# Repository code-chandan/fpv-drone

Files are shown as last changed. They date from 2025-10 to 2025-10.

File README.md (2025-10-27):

# Aero FPV Drone

Aero is that one FPV drone you design in your head during boring lectures and then actually build when you finally have the time and brainpower. It’s a freestyle rig that’s super lightweight, fully custom, and made to do flips, dives, and maybe crash a few times without crying.

This thing isn’t printed yet, btw. The model is locked and loaded in Fusion 360. 

---

## Frame Preview

| Image | Description |
|---|---|
|  | Full Fusion 360 render of the frame. All parts modeled to scale with 5" props |

---

## what came into my mind when i designed it

Aero was designed from scratch in Fusion 360 with the idea of keeping things modular, fixable, and crash-forgiving. The frame uses custom top and bottom plates that can either be 3D printed in PLA+ or laser-cut in carbon fiber if budget allows. The arms are separated for easier swaps when the inevitable faceplant happens. Every screw, standoff, and capacitor has its space.

It’s got that “I-built-this-in-my-room” energy but backed by a parts list that can punch with the big brands. The wiring is gonna be clean thanks to the 4-in-1 ESC stack, and the VTX and analog cam give it old-school FPV vibes without sacrificing clarity.

---
## diy transmitter and receiver 

| Image | Description |
|---|---|
|  | diy transmitter |

| Image | Description |
|---|---|
|  | controller case |

| Image | Description |
|---|---|
|  | diy receiver  |

| Image | Description |
|---|---|
|  | flight controller ( more layers cus so much routing) |

---
## Tech Specs

- Motor-to-motor distance fits 5-inch props  
- 2207 2400KV motors 
- 4-in-1 ESC (30A) with solder tabs facing up  
- Power distribution through a separate PDB  
- XT60 battery input with a 470uF cap for that ripple control  
- GPS module slot for Return-To-Home  
- Space for analog FPV cam + VTX  
- Foam landing pads and battery strap support

---

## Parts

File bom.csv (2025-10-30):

Product | Price per Unit | Qty | Estimated Price (USD) | Link
2207 2400KV brushless motors | $13.63 | 4 | $54 | https://robu.in/product/sunfun-d2207-2600kv-bldc-motor
4-in-1 ESC 30A | $35.00 | 1 | $35.00 | https://robocraze.com/products/speedybee-f405-bls-50a-30x30-4-in-1-esc
PCB(JLCPCB) | $154 | 1 | $154
Arms (petg-cf)(own expense) | NIL | 4 | NIL
Top Plate (petg-cf)(own expense) | NIL | 4 | NIL
Bottom Plate (petg-cf)(own expense) | NIL | 4 | NIL
M3 Screws | $6.00 | 1 | $6.00 | https://robu.in/product/easymech-ss-304-pan-philips-head-m3-x-5-mm-bolt-25-pcs
5-inch Tri-blade Props | $2 | 4 | $8.00 | https://robocraze.com/products/9450-carbon-fiber-propeller-for-f450-f550-drone-1-pair
XT60 Connector | $1.20 | 1 | $1.20 | https://www.amazon.in/Invento-8944638611431-Female-Connectors-Battery/dp/B06Y6NRP5T
Power Distribution Board | $4.00 | 1 | $4.00 | https://robu.in/product/cc3d-power-distribution-board-dual-bec-lc-filter-led-switch
Capacitor (35V 470uF) | $2.50 | 2 | $2.50 | https://amzn.in/d/glLVvrR
Battery Strap | NIL | 1 | NIL
LiPo Battery 4S 1500mAh 100C | $19.97 | 1 | $19.97 | https://amzn.in/d/bcKfxz0
Video Transmitter (VTX) | $23 | 1 |  | https://robu.in/product/hglrc-zeus-nano-vtx-350mw-16x16-20x20-25-5x25-5mm
Antenna (VTX) | $7.11 | 1 | $7.11 | https://www.drkstore.in/flywoo-5-8ghz-light-5-8g-3dbi-brass-antenna-ufl-for-vtx/
GPS Module | $20 | 1 | $20 | https://www.drkstore.in/flyfishrc-m10-mini-gps-module/
Buzzer with LED | NIL | 1 | NIL
Foam Landing Pads | NIL | 1 | NIL
Heat Shrink Tubing | $4.00 | 1 | $4.00 | https://robocraze.com/products/530-pcs-color-shrink-tube-wire-insulation-sleeve
Silicone Wires (14AWG, 20AWG) | $3.00 | 1 | $3.00 | https://robocraze.com/products/xt60-female-connector-with-silicon-wire
Flight Stack Mounting Grommets | $1.50 | 1 | $1.50 | https://amzn.in/d/hn6yIDM
TOTAL |  |  | $262

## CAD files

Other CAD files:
cad/aero.step
cad/aero controller.f3d

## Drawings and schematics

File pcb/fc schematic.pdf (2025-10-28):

# GND¹

## SWD ¹

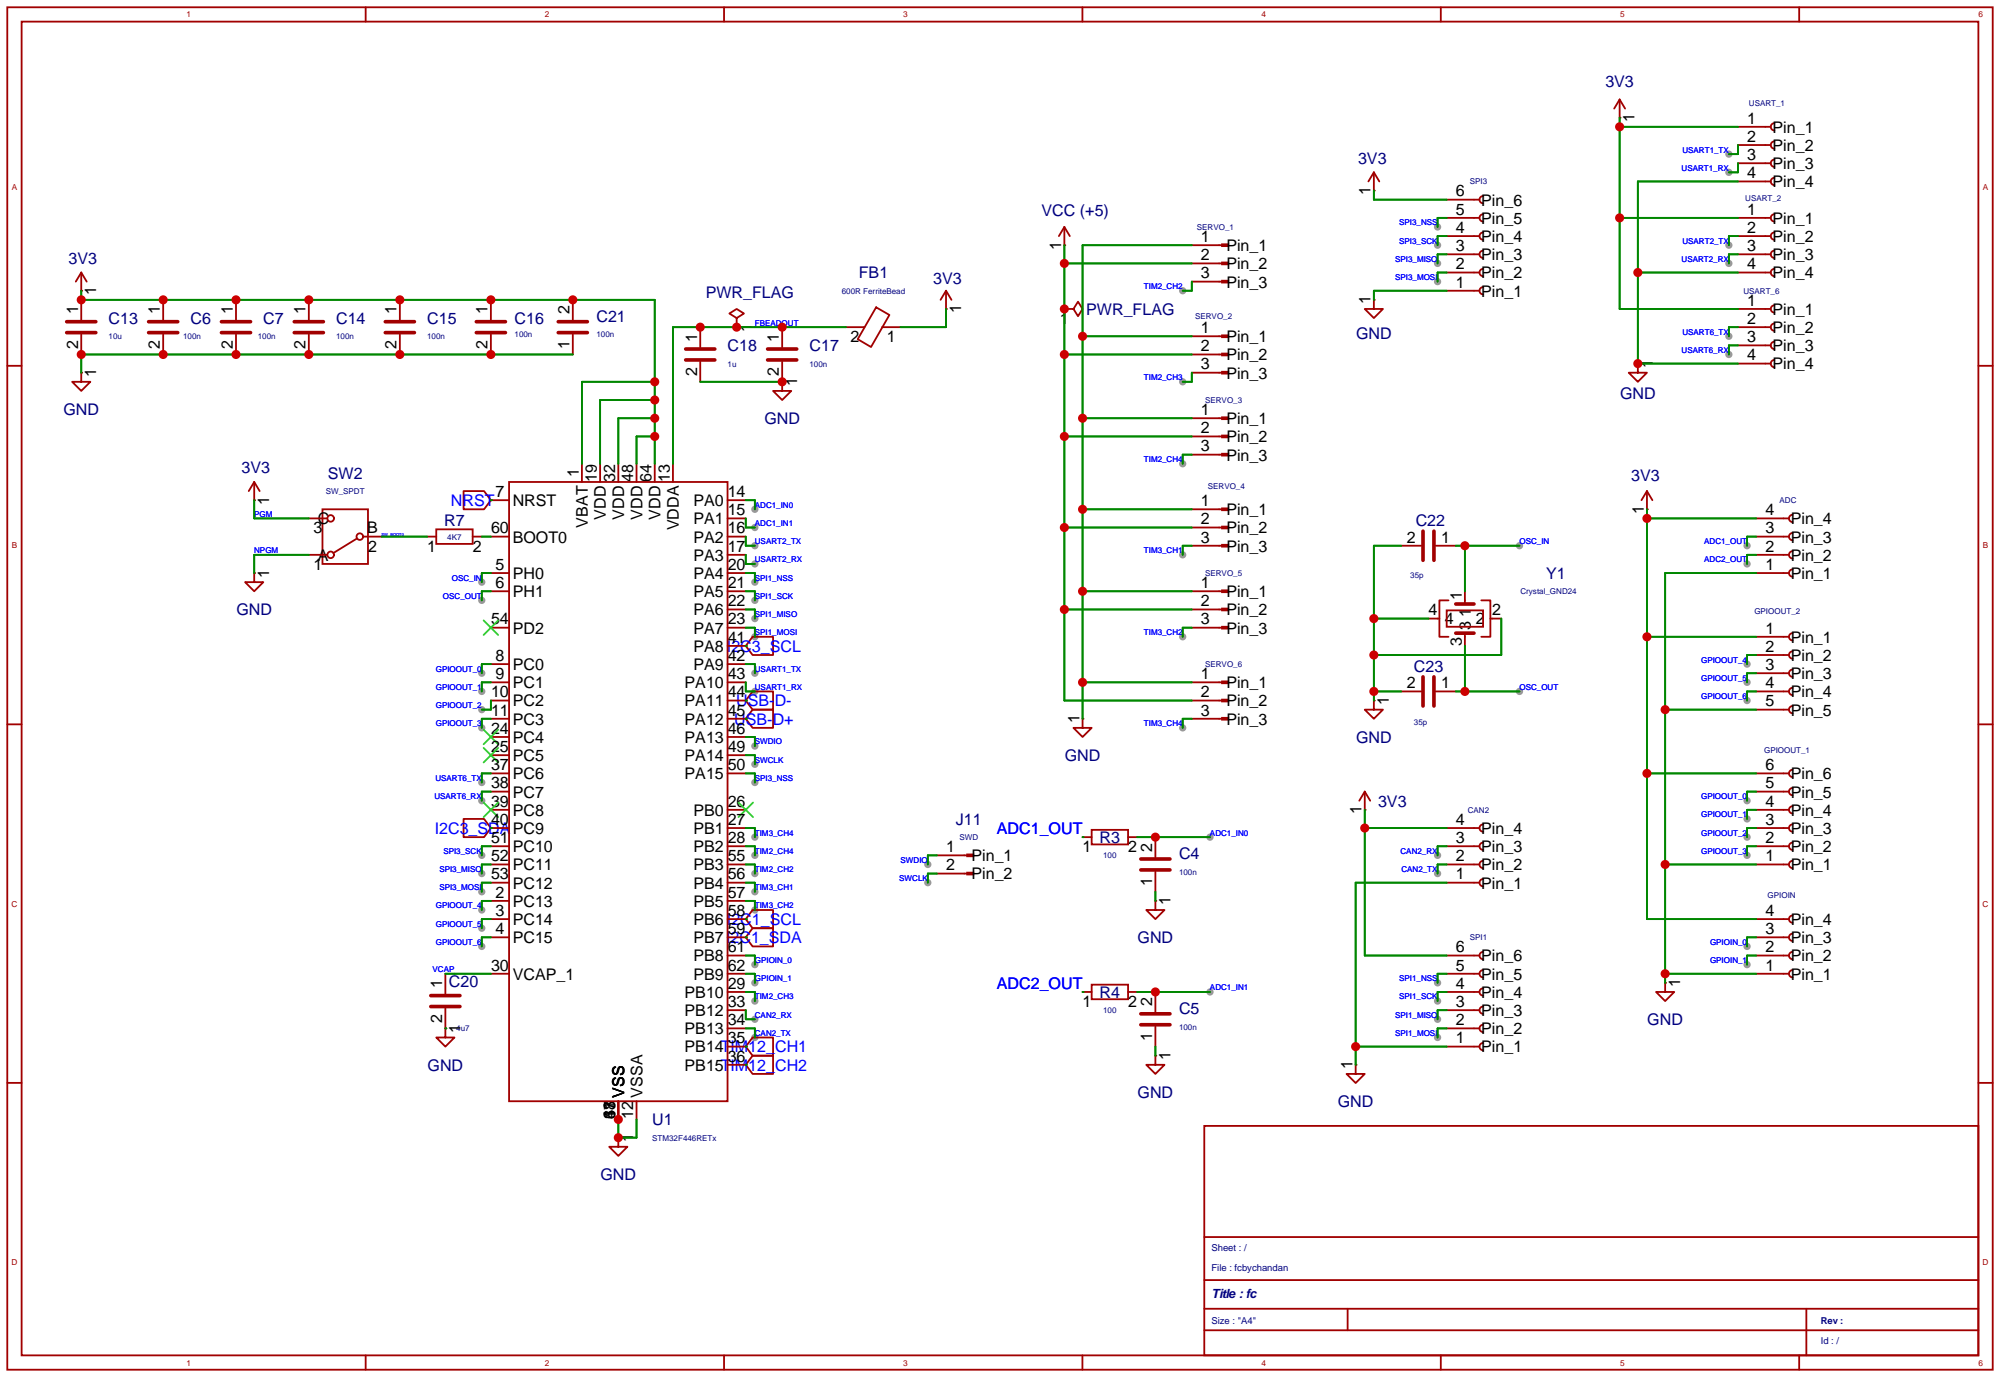
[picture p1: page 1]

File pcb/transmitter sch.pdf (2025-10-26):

## GND³.3V

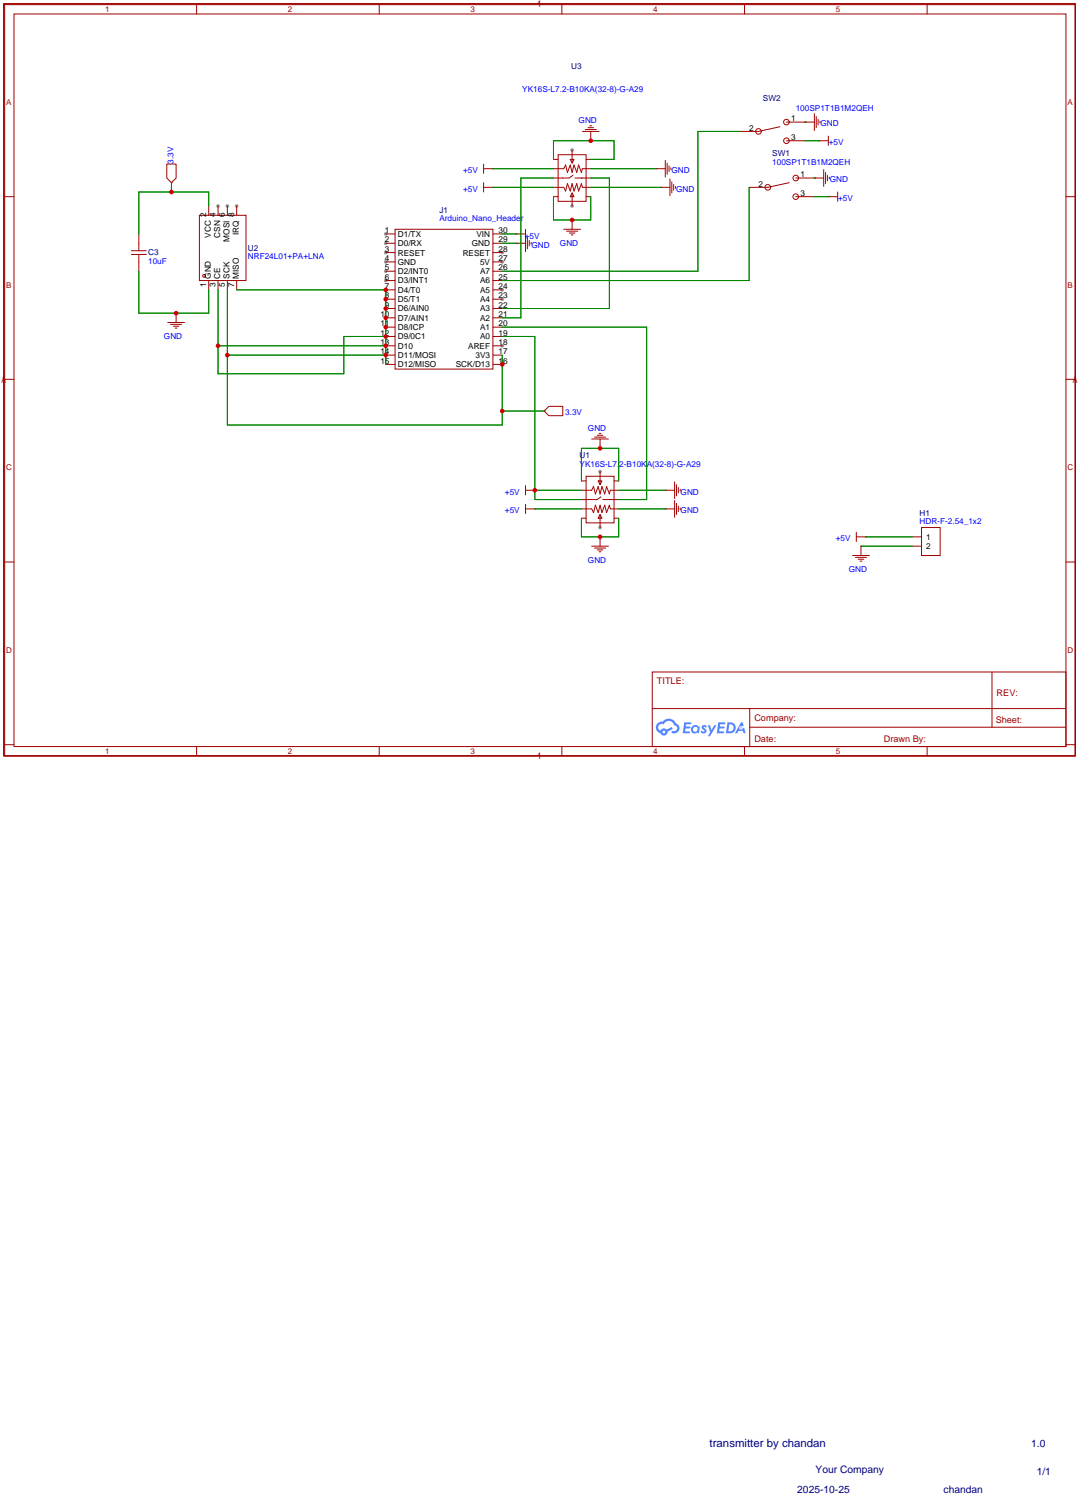
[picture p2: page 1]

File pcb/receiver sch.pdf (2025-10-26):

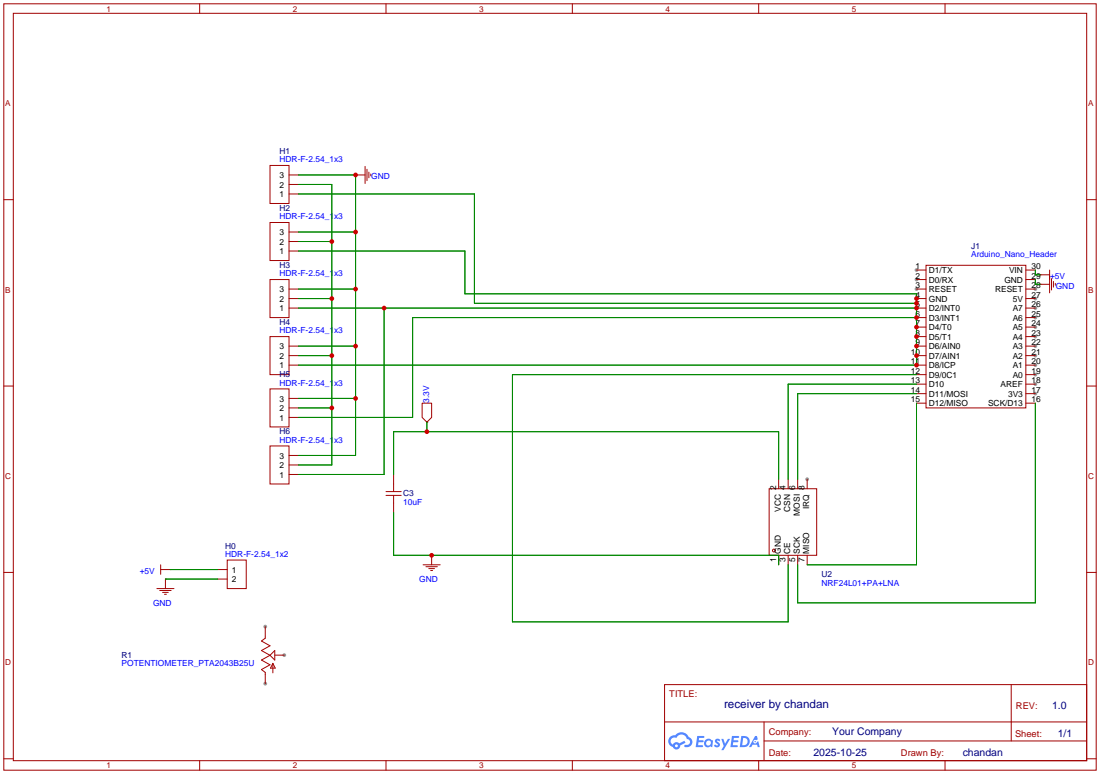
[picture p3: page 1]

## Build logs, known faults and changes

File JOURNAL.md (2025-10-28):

<!--
  ===================    !!READ THIS NOTICE!!   ====================
  DO NOT edit this file manually. Your changes WILL BE OVERWRITTEN!
  This journal is auto generated and updated by Hack Club Blueprint.
  To edit this file, please edit your journal entries on Blueprint.
  ==================================================================
-->

## 10/23/2025 1:19 AM - First sketch of arm  

Kicked things off with a rough sketch of one drone arm. Kinda freestyled it at first just to get the proportions right. It’s giving low poly energy but it’s fine for now. Started defining anchor points, main circles, and a flat reference. Just wanted to see something on screen ngl. Didn’t go too deep. Mostly just sketch and vibe.arm sketch.png

## 10/23/2025 1:25 AM - Added dimensions and holes  

Went full nerd and started dimensioning everything. Dialed in the hole placements to ±0.01 mm. The arm got some realistic mounting holes too. I used the "Fix" constraint like a cheat code. The goal was making one arm perfect so I can mirror it later. Honestly, this part was surprisingly fun, takes a hell lot of planning to do such a small thing :sob:main body.png

## 10/23/2025 1:29 AM - Mirrored full arm layout  

Time to go symmetric. Mirrored that one finished arm into four. Boom X-frame instantly. Seeing it all align felt good. I tweaked a bit to keep everything smooth and centered. Even added mid-line constraints to avoid future chaos. Very chill but satisfying work session.solid body.png

## 10/23/2025 2 PM - Finalized arm + center  

Today was clean-up and contour day. I cut a neat circular slot in the center and shaved off weird edges. Played around with how the arms curve into the center plate. Tried to keep it modular so one break doesn’t destroy the whole thing. Saving this design now felt way more solid.finalized arm + center.png

## 10/23/2025 3 PM - Arms joined to center plate  

Assembled the center + arm units for the first time. Arms looked sharp. Made sure each arm was removable. Spaced things out so M3 screws could fit in nicely. I think we’re officially in the “it looks like a drone” phase. Had to fix a few weird shell merge issues too.Arms joined to center plate.png

## 10/23/2025 4 PM - Overlapping fix + cleanup  

The overlapping bits between arm and mid-plate were bugging me. So I made a clean cut that fits like a socket. No glue or junky fits needed. Played with clearance values too. Hoping this makes disassembly a breeze in the field. Bonus points for modularity.Overlapping fix + cleanup.png

## 10/24/2025 5:03 PM - Adjusted arms and motor holes  

Revisited motor mount designs after checking motor specs again. Standardized everything around a 23mm M2 bolt pattern. Realized I forgot to offset the motor cable exits fixed that too. Pretty confident the frame arms are done unless someone finds a flaw.

Adjusted arms and motor holes.png

## 10/24/2025 5:05 PM - First assembly + mounts  

Stacked in the standoffs to complete the sandwich design. The frame started to look like it came off a store shelf. Gave it more volume, added screw holes to lock the standoffs into the plates. No flex no wobble. Can’t wait to slap components on it once it's printed.

First assembly + mounts.png

## 10/26/2025 12:26 AM - Final modular frame render  

Final render. Final sanity checks. Did a full dry run of what components will go where. Sent over screenshots to friends for peer feedback. Thinking of getting it CNC’d instead of 3D printing now. Frame’s 100% ready for slicing but still waiting on project grant approval.

frame render

## 10/26/2025 12:38 AM - transmitter pcb  

I spent today working on the transmitter board, which is the main controller for the drone. Pitch, roll, yaw, throttle, and all other significant signals sent to the receiver are all controlled by it; in other words, it controls every facet of flight control.

It was made to look like a handheld controller, which makes it comfortable and simple to use. I also added a custom silkscreen with my tag just a small signature to show that I built it.

I spent some time fine-tuning the schematic before starting layout to ensure that every connection, switch, and potentiometer mapped to the control logic. Having a clean schematic made it much simpler to keep the wiring organized while building the PCB. I'm quite happy with the way the blueprint is developing so far.




## 10/26/2025 11:32 AM - made the receiver board  

The FPV drone's receiver board was ridiculously tiny, so I had to be very careful with the layout. I built everything else around the antenna module after I had it installed. It was like solving a puzzle with traces. kept the power lines neat and thick while carefully packing the signal traces into the remaining areas. Filtering capacitors were placed close to the data and power input lines to cut down on noise.

Worked hard on the schematic as well; double-check all connections, label everything clearly, and ensure that the layout exactly matches the schematic. The board is one of the cleanest I've made so far, despite its small size.receiver pcb



## 10/26/2025 11:34 AM - designing the fc pcb  

The flight controller (FC) PCB design was, to be honest, the most difficult part of the build so far. Because this board connects everything ESCs, receiver, gyro, USB, and power the routing soon became complex. I started by placing the MPU and MCU dead center to preserve balanced trace lengths and unobstructed signal paths.

Before beginning layout, I spent a fair amount of time working on the schematic, making sure that all of the connections, pin mapping, and component labels were perfect. When the schematic was clean and organized, 

fc pcb



## 10/26/2025 11:48 AM - controller case design  

The design of the controller case turned out to be much more challenging than anticipated.  Without becoming a brick, this section needed to balance internal space, ergonomics, and clean aesthetics.  I began by setting up the joysticks because everything else is centered around them.  The top shell was then sculpted to preserve the comfortable angles and organic grip.  Primarily functional, the lower part offered enough depth for PCB mounts, wiring, and connectors.  To align the mounting holes and make sure the top and bottom closed flush, multiple test fits were required.  I ended up chamfering the edges a little to give it that crisp, machined feel.controller case

## 10/28/2025 - updated the cart prize of jlcpcb cart  

I accidentally submitted the JLCPCB cart with a PCB thickness of 2mm instead of the required 1.6mm. Even though I hadn't noticed it at first, I was lucky to find it before everything was finalised. It should continue to be lighter and more mounting-standard now that I've switched back to 1.6mm.

I have also added pictures of the schematic, included two screenshots of the JLCPCB cart, and improved the detail of my journal entries for appropriate documentation. I feel more organised now that I have the build logs.

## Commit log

2025-10-27 added aero CAD files using git lfs
    [aero controller.f3d, aero.step]
2025-10-28 added fc schematic to the repo
